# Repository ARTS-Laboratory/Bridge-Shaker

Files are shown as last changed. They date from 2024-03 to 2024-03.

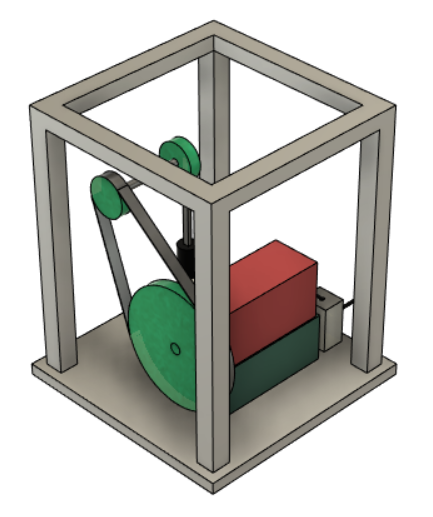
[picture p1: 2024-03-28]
images/design_view2_v2.png

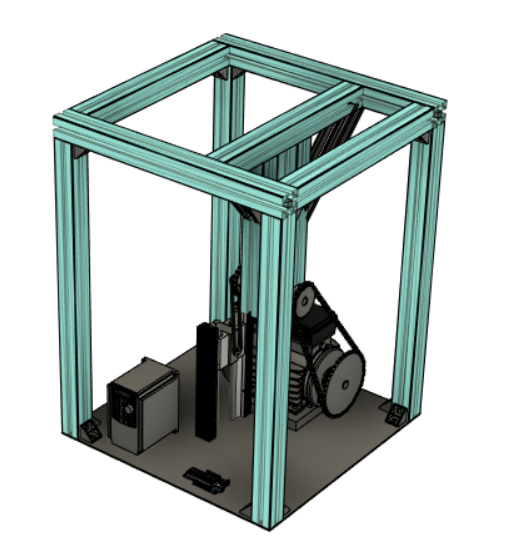
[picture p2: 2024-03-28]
images/assembly_v2.png

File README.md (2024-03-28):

# Bridge-Shaker

A modal shaker for bridges created by the May 2023 Downey1 senior design team.

## CAD files

STEP files of each component of the bridge shaker. Created in Fusion 360 2023, printed with Cura.

## images

Pictures of CAD assembly.

## model

Simulink model of bridge shaker.

## reports

All reports for Senior Design I and II.

## test_data

Data from bridge shaker on 300 main bridge with accelerometers. Tests were performed at 5 Hz, 10 Hz, 11 Hz, 15 Hz, and 20 Hz

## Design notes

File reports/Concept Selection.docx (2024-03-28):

Concept Selection

1. Introduction

The purpose of concept selection is to evaluate each previously generated concept and determine which is the most viable to advance in the design process. The significance of concept selection is that it utilizes empirical measurements to select the best concept for the customer without interference from designer biases. This report presents a matrix-based down-selection of each concept using previously identified selection criteria. First introduced is the concept screening process, which assesses positive or negative concept criteria performance relative to a baseline concept. Once concept screening is completed, this report advances to the concept ranking, which assigns quantitative values to the positive/negative performance of the top concepts from the concept screening. Finally, the chosen concept is presented as the design the team plans to advance to fabrication. All referenced concepts are provided in the appendix and are referenced by their numbers throughout the report.

2. Concept Screening

The concept selection matrix’s main function is to narrow down the options by eliminating concepts that score too low in addressing customer requirements. The selection criteria was based on the customer requirements formulated in the Functional Decomposition and Concept Generation report. Each concept was rated relative to the reference, concept 1, to decide which concepts would be desirable to move forward with. The reference concept was decided unanimously among the group to be the best “middle path” due to its simplistic design and intuitive nature, but other concepts could outperform it due to issues inherent with a spinning weight on a moment arm. In the matrix, a "+” indicates that the given concept would outperform the reference in the customer requirement, while a “-” indicates it would underperform in relation to the reference. A “0” means that it would perform the same as the reference concept. It should be noted that when the table was first created, more selection criteria existed (as shown in the Needs Metrics Matrix in the appendix) but were removed due to similar performance across concepts. This would have given a result of “0” along the entire column, and therefore would not have had any factor in changing the comparative scores. The results of each concept performance are shown in Table 1.

Table 1: Selection Matrix

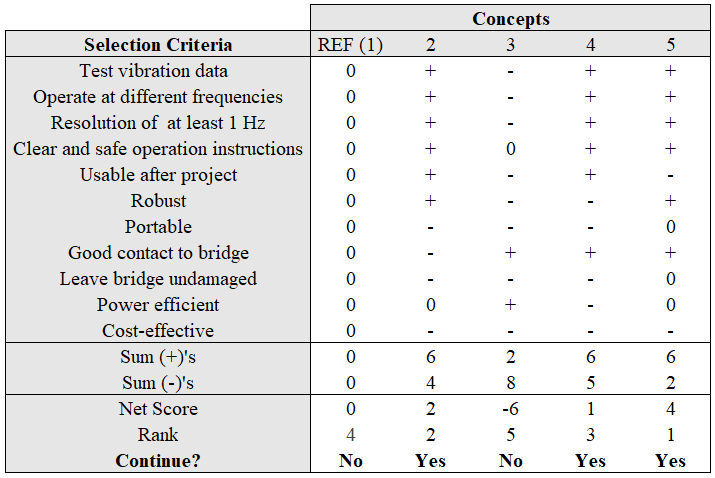
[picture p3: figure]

The final score for each concept was calculated by subtracting the sum of “-”s from the sum of “+”s. The concepts were then ranked based on these scores and the top three scoring concepts moved on to the second round of concept ranking. The ratings were given based on analysis and a vote of each group member comparing each concept with the reference. The top three concepts based on Table 1 are concepts 2, 4, and 5. Concept 2 is the design with solenoids inducing vibration, concept 4 is the hydraulic actuator-based design, and concept 5 is the linearly oscillating weight that is moved up and down with a crank. Concepts 1 and 3 did not have a high enough score to move on to the second round. Concept 1 underperformed in multiple areas, including contact to bridge and operating at different frequencies. Concept 3 underperformed in the categories of clear and safe operation instructions and resolution of at least one Hertz.

3. Concept Ranking

The top three out of five concepts proposed were used to create a concept ranking matrix to condense the list of possible candidates for a final concept. The concept ranking matrix would further derive which design was the best to move forward with. Each concept was given a rating between 1 and 5 based on how well it meets each selection criterion of the project. A rating of 5 indicates a significant improvement from the reference design while a 1 indicates a severe deficit. The importance weight factor was determined by the team in the product specifications report with the Needs Metrics Matrix. The importance weight factors were normalized across the selection criteria (see appendix for normalization formula) and multiplied with the rankings, resulting in a weighted score for each criterion. All the weighted scores for a concept were added together for a total score. The highest total score would be the concept deemed the best to move on with for the project. Table 2 shows the concept ranking matrix and concludes that concept 5, a linear weight with a DC motor, is the best option due to its vast improvement on the reference.

Table 2: Concept ranking with importance weight factors.

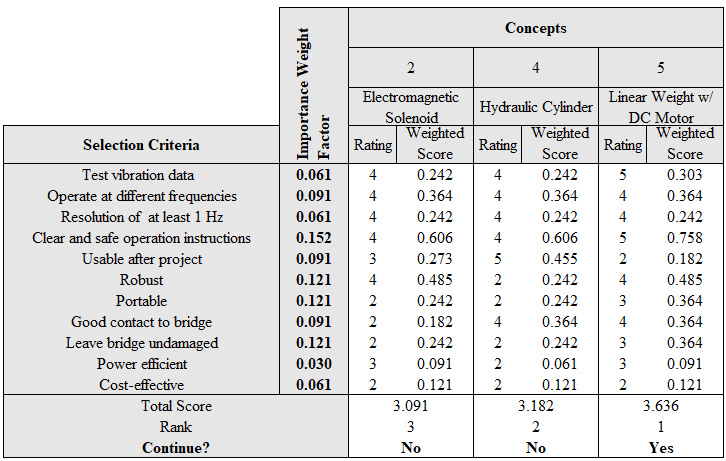
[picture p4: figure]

It was decided that the linear weight with a DC motor would test vibration and be easier and safer to use than the other concepts. The highest importance weight factors corresponded to the clear and safe operation instructions, robust, portable, and leave bridge undamaged selection criteria. Concept 5 ranked higher relative to the other concepts in three out of four of these categories, which explains its higher total score and designation as the best concept.

4. Final Concept

The concept selection tables designated the highest-scoring concept as the best design. Concept 5, the linear weight powered by a DC motor shown in Figure 1, scored highest in both tables because of its ability to test vibration data at a wide range of values, as well as the ability to transfer energy more efficiently to the bridge.

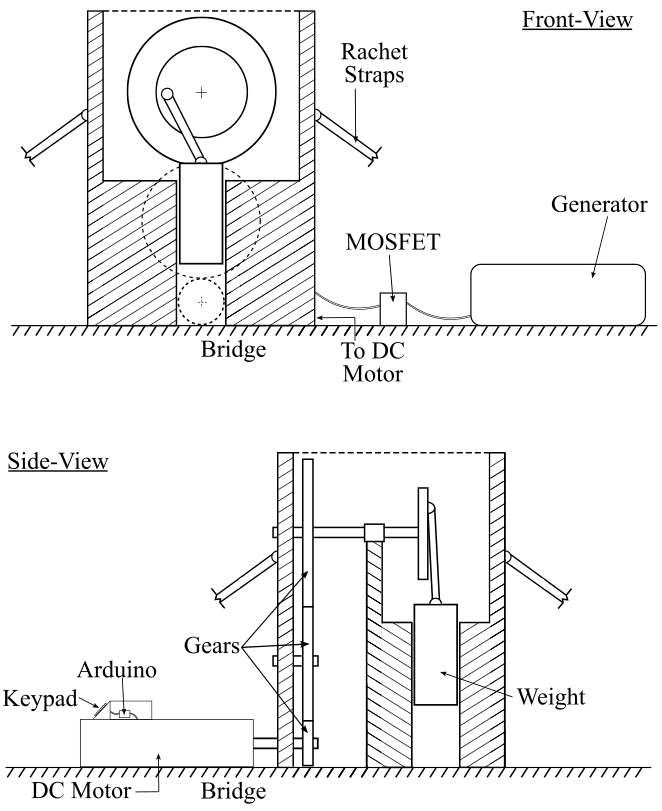
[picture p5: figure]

Figure 1: Excitation via DC Motor and powertrain for linear actuation.

The generator will provide enough power to the system while still maintaining an ease of portability. The MOSFET will control the flow of power from the generator to the DC motor and Arduino. Desired values for frequency and time can be input via the keypad, and the Arduino will control the speed to match the desired frequency. The energy of the DC motor will be translated through the gears and into the weight to create a linear motion, which will transfer downwards via the shaker’s weight into the bridge, inducing vibration. In an interview with stakeholder Joud Satme, he expressed concerns about concept 1’s ability to transfer energy from the shaker into the bridge and how rotational motion would be less efficient because forces were being exerted everywhere around the radius of the weight. Concept 5 can do this more efficiently by using gears to move a weight up and down to localize and create a one-dimensional force. This force would be better suited for testing vibration data because there is minimal wasted energy. This design is more complicated than some of the other concepts, but when evaluating the criteria for a productive shaker, concept 5 prevailed. The power train will add elements of difficulty in the design process, specifically trying to find an efficient gear ratio to excite all frequencies needed while not stalling the motor. To address this challenge, the team will source outside expert advice on gear train design, as well as create prototypes of gear ratios for experimental testing.

5. Appendix

Needs Metrics Matrix

Concept 1

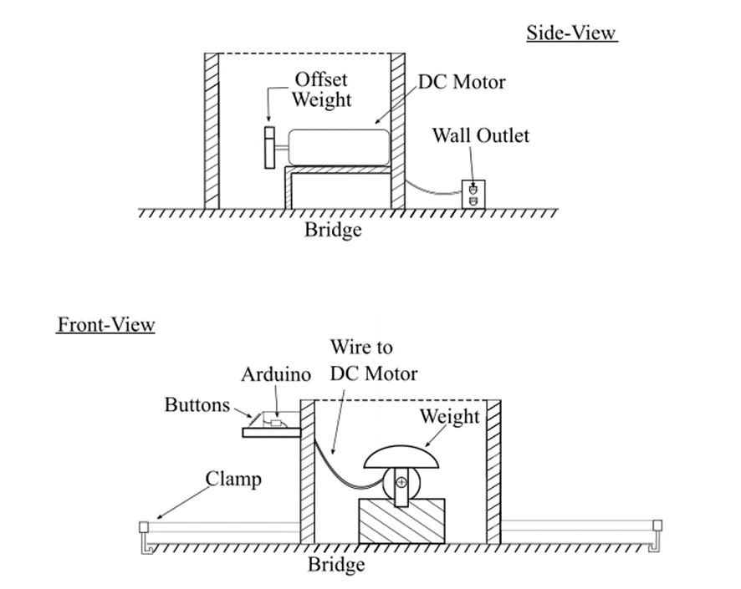
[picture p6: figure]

Concept 2

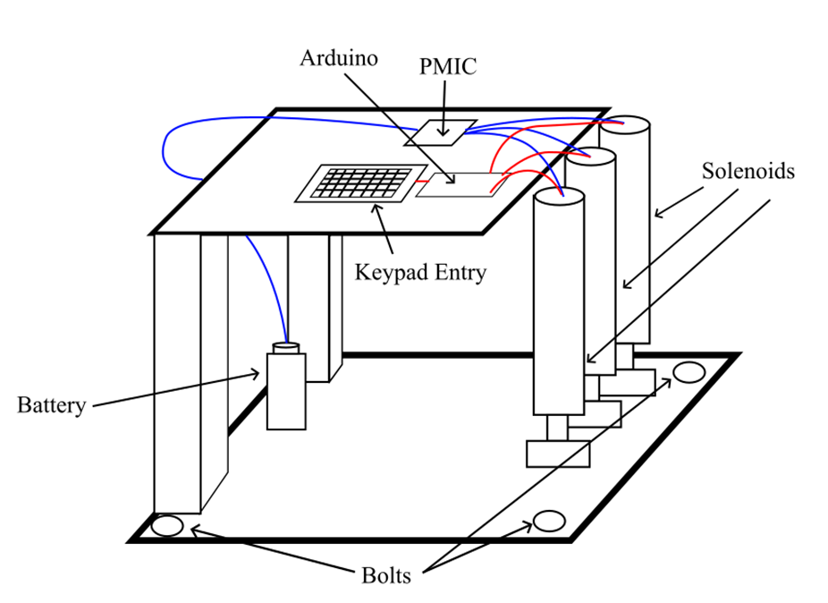
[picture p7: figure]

Concept 3

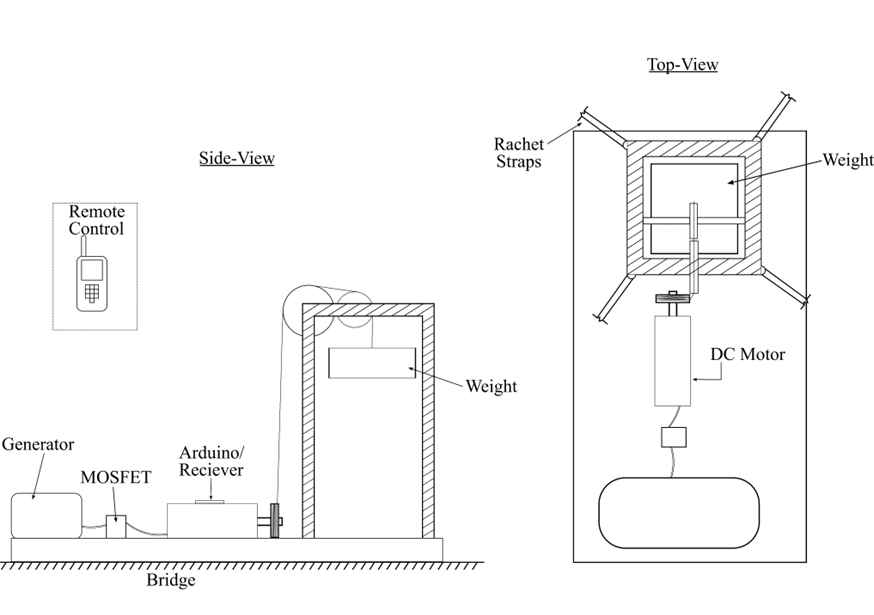
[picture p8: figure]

Concept 4

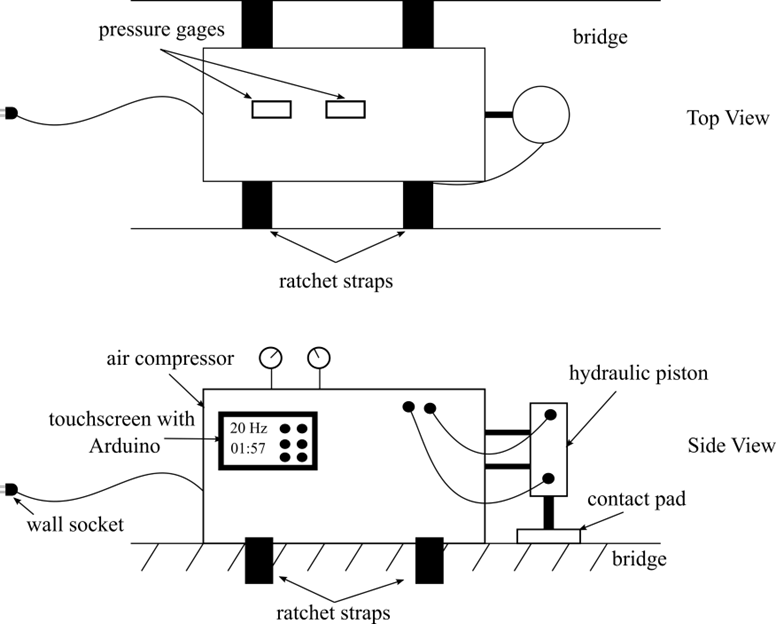
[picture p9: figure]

Concept 5

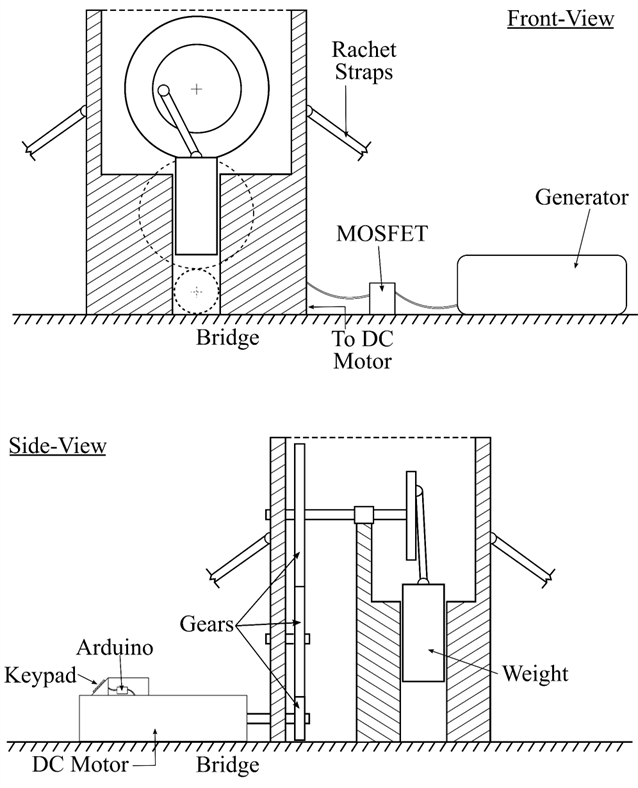
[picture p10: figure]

Normalization Formula

Importance Weight Factor= (Individual product specification weight factor)/(Sum of all product specification weight factors)

Downey1Concept Selection Process and Report11/04/2022

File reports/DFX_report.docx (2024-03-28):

Design Refinement

1. Introduction:

This DFX chapter entails this project’s specific design goals, including the design for manufacturability and assembly, cost, safety, the customer requirements, ease of use, durability/reliability, and serviceability. The design refinements which are being processed entail primarily the assembly and ease of use for the mass shaker. The assembly requires precise, accurate measurements along with the dimensions of the screw fasteners and brackets. Ease of use for the system comes down to programming the VFD and the visual data which will be displayed to the user via tachometer sensors for the shaft holding the weight. Manufacturability is vital because the shaker needs to be assembled and produced within a reasonable amount of time. The cost is also an important part of the design because we cannot go over budget, therefore the group has been using many parts readily available in the ARTS lab. Safety is arguably the most vital requirement, due to not only preventing injury to users of this project in the future, but also avoiding possible liability involved. The reliability/durability and serviceability of the bridge shaker go hand in hand. This project is planned to last without needing servicing for several years (3-5), thus robustness with the sourcing of quality parts is key to this project's success within the ARTS lab. The serviceability for the shaker will be dependent on the methods of securing the parts together, and whether the parts sources will be available in the future.

2. Design for Manufacturability and Assembly

To optimize manufacturability, the team considered material selection and connector design. Off-the-shelf parts were chosen in order to ease sourcing, and parts were chosen considering both cost and replaceability. 8020 40 series extruded aluminum in was chosen due to its ease of assembly. The 8020 series includes support brackets, connectors, beams, and fasteners that are compatible with each other to facilitate the manual assembly process by reducing the number of specialized parts and sourcing as many parts from one company as possible. The main trade off here is that 8020 extruded aluminum is more expensive due to its specialized design, and all connectors will have to be 8020 connectors to pair properly with the beams. The four corner connectors were 3D printed following an 8020 connector CAD model in order to reduce costs and weight; however, the team decided to perform poka yoke on the connectors since they were being printed. Guide channels were added to reduce the stress on the plastic from the screws and make assembly easier by keeping beams in place. In order to ensure the vertical beam is all the way down, the guiderail for the vertical beam was extended so that the two lateral beams would not be placed too far in and obstruct the vertical beam. Figure 1 illustrates the changes made to the brackets. A key tradeoff here is the time required to print the connectors, as well as the reduced strength of PLA versus aluminum.

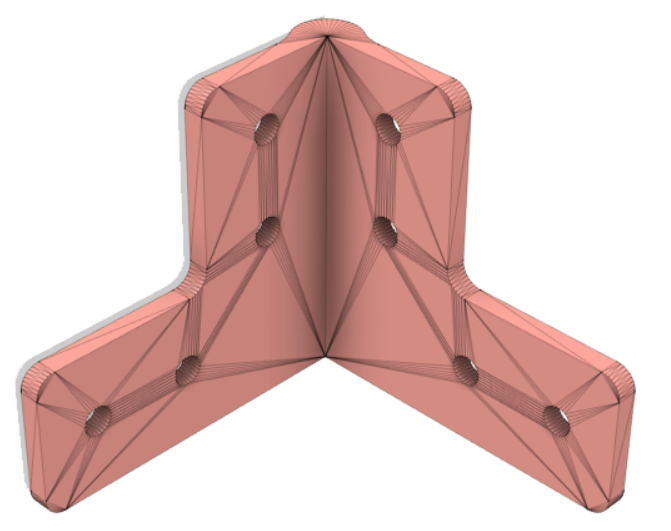
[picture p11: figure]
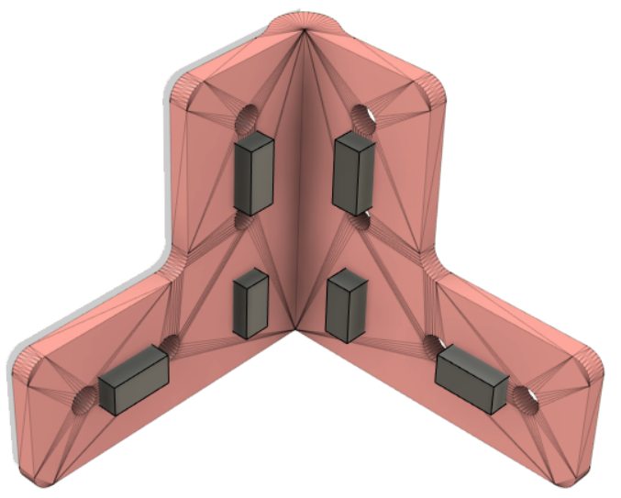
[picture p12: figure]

Figure 1. 3D printed bracket with only spine modification (left) and 3D printed bracked with poka yoke guiderail design.

3. Design for Cost

Cost was a limiting factor for the design team when coming up with ways to produce the shaker for Dr. Austin Downey. Inflationary reasons have made some parts of the build extremely expensive to buy and alternatives had to be sourced out. For example, non-name brand microcontrollers were purchased for the computation of the data and a VFD (Variable Frequency Driver) was sourced from Amazon instead of a big-name product. This saved a few dollars throughout but ultimately ended up reducing the gross amount spent more than expected. Another way the team designed for cost was by trying to use aluminum parts rather than steel parts. The ARTS Lab had an abundance of extruded aluminum for the team to use that reduced the frame production cost to $0. A similar approach was taken to the motor and the brackets. The motor was recycled, with permission, from one of the older projects that are stored in the sub-basement of 300 Main St. This three-phase motor would have been $400-700 (gathered from online stores while sourcing motors) off the shelf, instead the group spent no money on it. Since the brackets for the frame have been designed and 3D printed, the cost for each bracket went from $10-20 apiece, down to virtually $0 thanks to the ARTS Lab’s stockpile of PLA plastic. Lastly, an element of purchasing that saved a fair amount of money was sourcing parts through Grainger and placing a bulk order. Grainger offers free shipping and on larger orders such as the one placed, it saved a favorable amount of money compared to other online parts stores in shipping costs.

4. Design for Safety

Operating a shaker that involves handling a weight through high voltage rotation poses significant safety concerns for any individuals within close proximity during usage. An identified concern is the potential for the vibrational mass shaker to become overly efficient and cause disintegration, thus projecting debris and the weight. To diminish this potential safety hazard, it is crucial to ensure that the shaker is securely mounted onto the bridge, withstanding any forces generated during operation without the risk of tipping over. The design team opted to stabilize the shaker with sandbags to guarantee operational safety. A further concern to consider is the possibility of encountering electrical issues. If the electrical components, namely the motor and VFD, are not correctly wired and grounded, the vibrational mass shaker could pose a potential electrical shock hazard. To preclude these electrical risks, the design team conducted thorough research on wiring diagrams and component datasheets to ensure that all components were appropriately grounded and correctly wired. In order to prevent any of these safety concerns from ever becoming a problem, regular maintenance and inspection of the shaker and its components should be performed to ensure proper operation and determine any potential safety hazards.

5. Design for Customer Requirements

The goal of this project is to design a bridge shaker for Professor Austin Downey and the ARTs lab that will be used to test vibration data by operating at different frequencies. It must be safe to operate and leave the bridge undamaged. The mass shaker will induce vibrations via an oscillating weight which will transfer that energy to the bridge. The Needs Metrics Matrix, shown in Figure 2, has remained stagnant throughout the design and assembly process, with the most important engineering characteristics still being adaptability, usability by others, and product details. The contact area and weight of the shaker have been refined to have more emphasis on total product weight at the expense of the contact area, which will still be sufficient to transmit the force as the product will still be fully on the bridge, with the force increasing at the frame components in the base due to less material that would dissipate it.

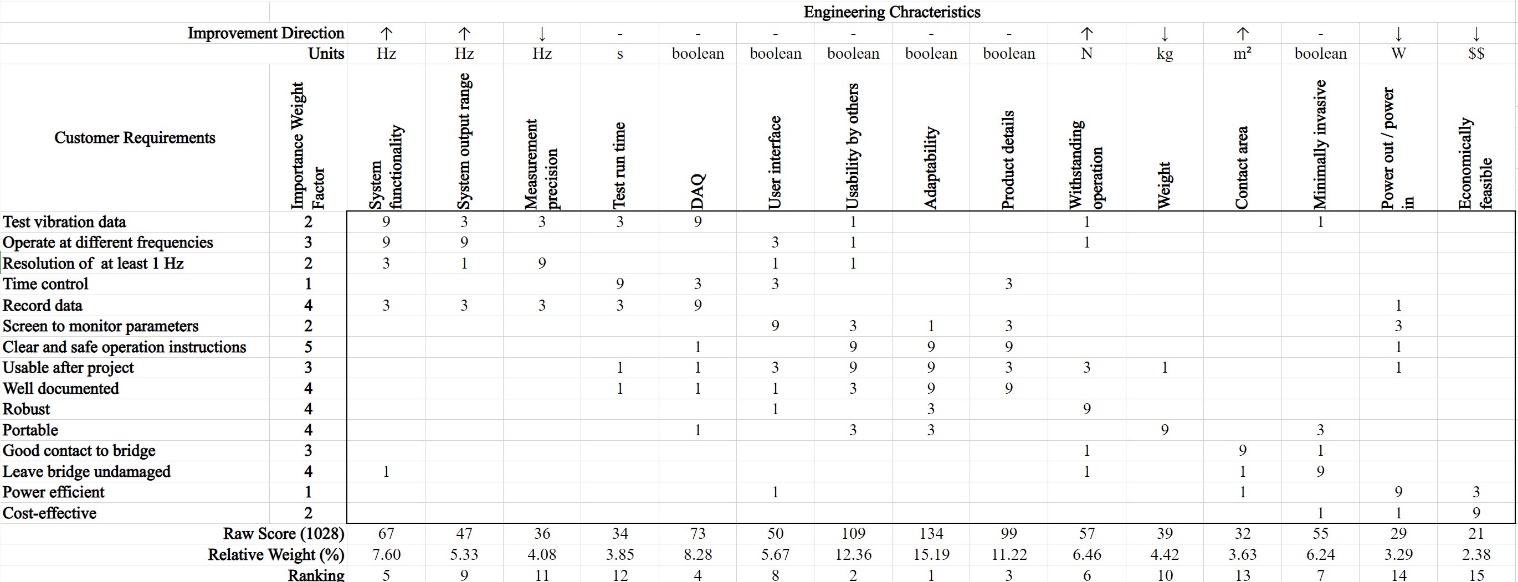
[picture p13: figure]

Figure 2. Needs Metrics Matrix shows the top engineering characteristics of importance along with customer needs.

5a. Design for Ease of Use

Ease of use was chosen because the Usability by Others EC was rated number 2 in the Needs Metrics Matrix. To enhance user experience, an external Arduino is added to clearly show the frequency and duration of the test. The VFD reads all user input to control the motor speed, but the data it shows is for the motor rather than for the weight. The external Arduino uses sensors to obtain and show the desired parameters for ease of use. The main tradeoff of having the Arduino is power consumption, as it requires extra power just for itself. Additionally, the shaker is entirely open-source with an extensive GitHub to promote user understanding and adaptability. The tradeoff of having the project open-source is that it would be less profitable in a market as competitors could recreate the design, but that is not a concern for the sponsor.

5b. Design for Durability/Reliability

To ensure the durability and reliability of the vibrational mass shaker, the design team prioritized the selection of high-quality materials and components. The frame of the shaker, constructed from high-strength 8020 series extruded aluminum, was chosen to withstand the significant forces exerted during operation and provide resistance to corrosion and wear. The metallic components, including gears, links, and weight, were similarly selected for their durability and longevity, with either steel or aluminum materials used. The 3-phase AC motor chosen for the shaker was a high-quality component that is expected to function optimally for the entire operational lifespan of the shaker. Coupled with a reliable and functional VFD, these components provide a robust and dependable vibrational mass shaker, which is engineered for long-term use.

5c. Design for Serviceability

The shaker will be a relatively violent machine that will attempt to vibrate itself into pieces. For this reason, the team attempted to minimize the parts used and design a shaker that was robust enough to remain strong even under the immense stress of the vibrations. With this comes the fear of part degradation or even failure. The team has sourced commercial products for the gears, shafts, frame, linkages, bearings, etc. this way anyone using the shaker after it has been commissioned can easily source a part to repair the shaker. Additionally, everything purchased, changed, or installed will be documented in a repository on GitHub that will allow for a new user to understand the device and be able to make simple repairs with ease. The only foreseeable serviceability concerns are with the motor and the VFD. These two items cannot be worked on explicitly like the other parts of the shaker. The VFD will have to be sourced out and purchased again if it were to break. The motor was recycled from an old project so it is likely that another motor would need to be sourced if the current one breaks.

6. Conclusions [and/or] Recommendations

Major refinements to this project mainly occurred in the layout and method of connecting parts to the frame, as well as refining the design of the brackets to increase robustness. Only minor changes were made to the sourcing of parts for the drive train, mainly the shaft and the sleeve which will be secured to the frame. The dimensions for the sprockets have remained constant, as well as the method of meshing them together via chains. The chain method will allow for flexibility of motor/sprocket replacement, especially if the dimensions of the motor or sprocket change. Further inspection of product safety may deem that the addition of surrounding walls for the shaker may be necessary in case of an unexpected failure in one of the moving parts. Tradeoffs have occurred primarily in the mass shaker’s base. While it needs sufficient contact to the bridge with a solid frame to place the components, too much weight on the bottom will ultimately affect the ergonomics of the product. An entirely metal base would also increase the price of the project, while providing no benefits to the wasted space. The method of stabilizing the shaker has also been changed from ratchet straps to sandbags on protruding extruded aluminum connected to the frame. This will give the shaker more vertical stability than the original horizontal, which is completely logical considering the acting force is strictly vertical. This method will also ensure the rachet straps wouldn’t end up pulling the shaker apart by slowly warping the frame, and users cannot accidentally over tighten them and break the shaker.

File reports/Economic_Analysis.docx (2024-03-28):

Economic Analysis

1. Introduction

Evaluating the economic gain or loss of a certain product is a vital aspect of engineering analysis. Ensuring that the product will have a net positive gain and not be a ‘money pit’ is done by evaluating the current assembly costs and operating costs coupled with the yearly expected expenses tied to maintenance and operation. The shaker being for Dr. Austin Downey and company has no industry value as this is a ‘one-of-a-kind' product that is designed specifically for the students who are testing the structural integrity of bridges and walking paths. The monetary value for this product can be estimated through the possibility of grants being offered to the students for research in this field. Given this fact, the break-even analysis, variable cost of labor, “year zero” cost, and the cost reduction analysis will be estimated using reasonable values. This analysis will also cover the expenses incurred and compare them to the expected future value of the parts most often replaced.

2. Costs, Savings, and Revenues

The bridge shaker being designed by Downey1 is intended to be an academic tool rather than a commercial product; however, the value of this shaker lies in the grant money that stands to be awarded by using the shaker for long-term vibration testing on large structures, something the ARTS Lab does not currently have equipment for. The costs are primarily from materials, as the labor required to build the shaker can be delegated to lab researchers. The cost for a single prototype is broken into fixed (materials, manufacturing/assembly) and variable costs below, and are modeled assuming the product would be commercially sold. This means that technician labor is estimated rather than researcher labor, and all parts are sourced from professional suppliers. Table 1 shows the fixed costs for a single bridge shaker based on the current prototype.

Table 1. Fixed costs per unit of current prototype.

Materials
Description | Cost (USD) | Quantity | Source
3 Phase AC Motor | 705.18 | 1 | Grainger
Industrial Chain | 29.55 | 1 | Grainger
Shaft pinion, 4" | 40.00 | 2 | Grainger
Motor gear, 8” | 64.58 | 1 | Grainger
Keyed Shaft: 1 in Dia, Aluminum | 52.63 | 1 | Grainger
Aluminum 80/20 40 series, 1 ft | 15.44 | 18 | Grainger
Elegoo Uno R3 | 17.99 | 1 | Bill of materials
LCD | 5.99 | 1 | Bill of materials
3pin IR Infrared Module | 1.89 | 2 | Bill of materials
OSH Park custom PCB for sensor input to Arduino UNO (shield form factor) | 23.55 | 1 | Bill of materials
Shaft bearings | 26.79 | 2 | Bill of materials
Extension cord | 25.98 | 1 | Bill of materials
Weight, aluminum 4 kg | 9.89 | 1 | Grainger
80/20 40 series fasteners | 1.54 | 100 | McMaster Carr
VFD, 230 Volts, 1 to 3 Phase | 118.84 | 1 | Bill of materials
PLA 3-way bracket | 2.52 | 6 | Cura 3D printer slicing estimate (101 g PLA per unit)
PLA triangle bracket | 1.42 | 20 | Cura 3D printer slicing estimate (57g PLA per unit)
Total: | 1666.98

Manufacture/Assembly
Description | Cost | Quantity | Source
Machining labor (2D cutting) | 20.00 | 2 hours | Wade 2022
Assembly labor | 18.81 | 5 hours | Indeed 2023
Total: | 134.05
Total fixed cost: | 1801.03

The total fixed cost per one bridge shaker is $1,801.03. It is important to note that for the shaker built by Downey1, many parts were able to be sourced for free, including the AC motor and Arduino. In the case of commercial production, this is a reasonable fixed cost considering the size and scale compared to other modal shakers. Table 2 displays the variable costs per year of the shaker.

Table 2. Variable costs per unit per year of current prototype.

Description | Cost | Quantity | Source
Maintenance | 18.81 | 20 hours | Indeed 2023
Operational electricity | 14.54/hr | 0.15 hours per test, assume 50 tests | Dominion Energy 2021 (0.021086 per kWh, at 690W)
Total variable cost: | 485.25

The total variable cost per year is approximated at $485.25. This estimate assumes 50 ten-minute tests per year and 20 hours of maintenance over the year by the same technicians responsible for the assembly of the shaker in the fixed costs. The predicted lifespan of the bridge shaker is 3 years, assuming proper pre-test maintenance (tightening fasteners, lubrication). Table 3 shows the up-front cost of the shaker.

Table 3. Up front (“Year Zero”) costs.

Description | Cost | Quantity
Research and development | 50.00/hr | 90 hours
Creality 3D printer | 236.00 | 1
Total Year Zero cost: | 4736.00

The up-front project costs total to $4,736.00 and are primarily the cost of design consulting with the team. The cost of the printer is included as an equipment cost, but the cost of the machine that manages 2D cutting of the aluminum is not included because the task is outsourced to machinists.

Table 4. Reduced cost of the materials for a version of the shaker.

Reduced Cost Version of Materials
Description | Cost (USD) | Quantity | Source
3 Phase AC Motor | 705.18 | 1 | Grainger (Dayton)
Industrial Chain | 15.32 | 1 | McMaster Carr
Shaft pinion, 4" | 40.00 | 2 | Grainger
Motor gear, 8” | 64.58 | 1 | Grainger
Keyed Shaft: 1 in Dia, Aluminum | 45.15 | 1 | McMaster Carr
Aluminum 80/20 40 series, 1 ft | 15.44 | 18 | Grainger
Elegoo Uno R3 | 8.96 | 1 | eBay
LCD | 5.99 | 1 | Bill of materials
3pin IR Infrared Module | 1.89 | 2 | Bill of materials
OSH Park custom PCB for sensor input to Arduino UNO (shield form factor) | 23.55 | 1 | Bill of materials
Shaft bearings | 26.79 | 2 | Bill of materials
Extension cord | 25.98 | 1 | Bill of materials
Weight, aluminum 4 kg | 9.62 | 1 | McMaster Carr
80/20 40 series fasteners | 1.54 | 100 | McMaster Carr
VFD, 230 Volts, 1 to 3 Phase | 118.84 | 1 | Bill of materials
PLA 3-way bracket | 2.52 | 6 | Cura 3D printer slicing estimate (101 g PLA per unit)
PLA triangle bracket | 1.42 | 20 | Cura 3D printer slicing estimate (57g PLA per unit)
Total: | 1635.97

Table 4 includes material cost reductions in terms of money on parts. It is important to note that the reduction is not substantial as the team was trying to optimize costs for the current prototype already. However, there were some significant optimizations when sourcing some materials, such as the keyed shaft, from McMaster Carr rather than Grainger. There are cheaper options for building a frame such as welding materials together, but the team found that unnecessary as the shaker would need to have the option to be taken apart. As sourcing cheaper materials will not change the cost of labor for assembly, the cost of assembly will stay the same at $134.05. This would bring the reduced total fixed cost to $1770.02, having around a 2% reduction in cost. An option for increasing longevity and reducing the need for maintenance would be to source aluminum brackets to replace the PLA. This would increase the cost of the triangle brackets from $1.42/bracket to $21.99/bracket and the 3-way bracket from $2.52/bracket to $10.99/bracket when sourcing from Amazon.

3. Analysis

Break-Even Analysis:

The bridge shaker is planned to be a viable tool in engineering work for 10 years. This period was chosen because at that point the research performed with the shaker will most likely be completed and the project will have turned a project in the break-even analysis, which was performed to determine when the revenue would surpass the cost along with initial startup. The following values were considered in Table 5.

Table 5. Break even analysis conditions.

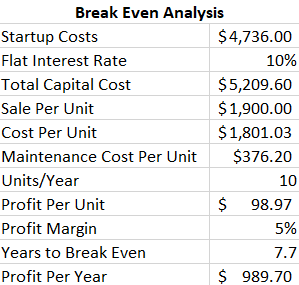
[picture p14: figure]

These values are assuming the shaker is relatively low demand, only producing 10 a year and requiring yearly maintenance for upkeep. The shaker’s price is set at $1,900, which makes about a 5% profit per sale. With these variables, Figure 1 shown below shows the method by which the break-even point was determined.

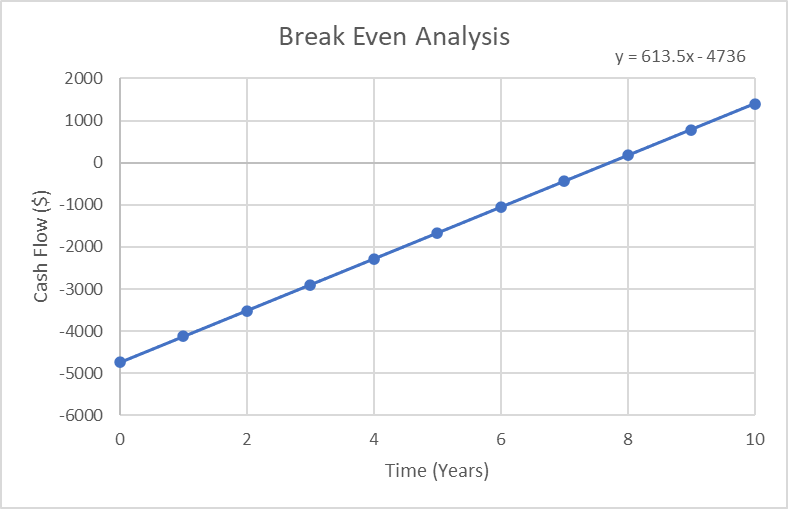
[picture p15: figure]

Figure 1. Break-Even Analysis

As shown above in Figure 1, the equation of the trendline can be used to estimate the year this project breaks even at 7.7 years. This is unfavorable as the use for this project is for short term research applications. The cash flow diagram of this project is shown below in Figure 2, with the initial cost of startup at year 0, and every year, having costs to produce 10 shakers a year. The profits each year come from the sales of 10 shakers each year.

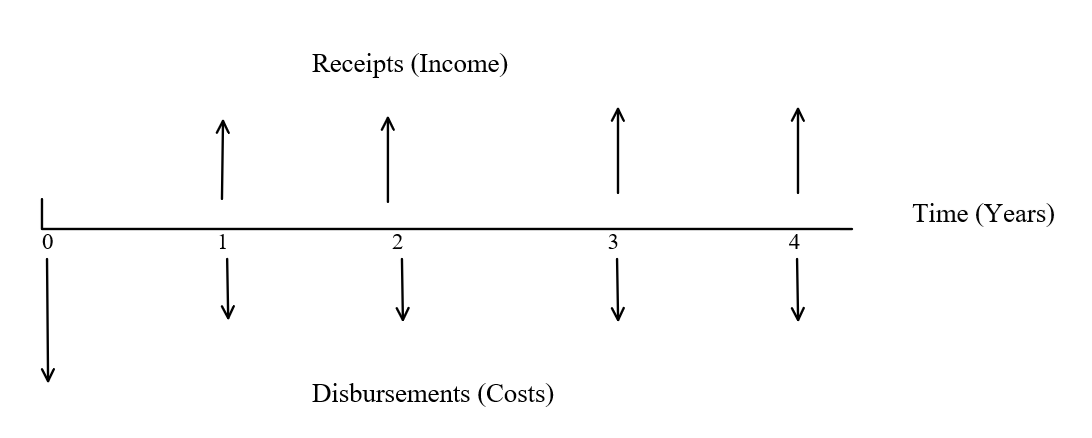
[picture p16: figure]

Figure 2. Cash flow diagram

Net Present Value:

The Net Present Value represents the difference between the present value of cash inflows and outflows over a specified period. It is used to analyze the profitability of the project over its life cycle/useful lifetime [4]. The equation used to determine the present value for each year is shown below as Equation 1.

NPV= ∑_(t=1)^T (C_t)/((1+r)^t)-C_o Eq.1

In this equation, NPV is the net present value, t is the period, starting at 0 and stretching over its life cycle until year 10, C_t is the net cash inflow of the period, r is the discount rate, and C_o is total initial investment cost. In order to find the discount rate, the NPV equation must be set to 0, and the other values are known besides r as shown below in Table 6.

Table 6. Values for the NPV Equation

Variable | Value
t | 10
C_t | 98.97 × 10
C_o | 4,736
NPV | 0

With these variables all know and r unknown, the discount rate can be calculated to be 14.5%. Finally, the NPV can be calculated as shown in Table 7 below.

Table 7. NPV Calculation

Net Present Value
| Project Time (Years) | 10
| Discount Rate | 14.5%
Year | Present Value
0 | -$4,736.00
1 | $5,600.37
2 | $5,490.91
3 | $5,395.31
4 | $5,311.81
5 | $5,238.89
6 | $5,294.66
7 | $5,119.59
8 | $5,071.01
9 | $5,028.59
10 | $4,991.53
Total Net Present Worth | $47,806.67

As shown above, the net present worth of the project can be estimated to be $47,806.67. This is a favorable outcome and could hold opportunity to be profitable. However, this project is not meant for something to be in mass production. While the sourcing of the parts was relatively easy, the fact of the matter is there is no way of knowing the demand for the product, which has means only to serve the ARTS lab in conducting experiments dealing with constant impulse-induced vibrations. While there could be universities that would like to fund this and may want to purchase a shaker for these reasons, there is no guarantee that the market would be there. Additionally, the shaker is designed to last for at least 10 years with relatively minimal maintenance besides replacements for parts which are under the greatest stress. Therefore, it is advised to keep this as a small scope project for the purposes of the University and research grants that come in for which this shaker can be used to aid in its development.

4. Conclusions/Recommendations

In conclusion, the bridge shaker is expected to be useful for three years until research is completed. A break-even analysis was conducted to determine when revenue would exceed costs by assuming low demand, a production rate of 10 units per year, and yearly maintenance. The shaker is priced at $1900, resulting in a 5% profit per sale. The break-even point is estimated to be 7.7 years based on the trendline equation.

List of References

1. Wade, A. O. (2022, September 20). How much does CNC cost per hour? www.remodelormove.com. https://www.remodelormove.com/how-much-does-cnc-cost-per-hour/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
2. ‌Indeed. (2023, March 15). Assembly technician salary in United States [Review of Assembly technician salary in United States]. Indeed. https://www.indeed.com/career/assembly-technician/salaries
3. ‌Dominion Energy. (2021, December 9). Schedule 1-Basic Residential Rate [Review of Schedule 1-Basic Residential Rate]. Dominion Energy. https://www.dominionenergy.com/-/media/pdfs/virginia/residential-rates/schedule-1.pdf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
4. Fernando, J. (2022, November 16). Net present value (NPV): What it means and steps to calculate it. Investopedia. Retrieved March 20, 2023, from https://www.investopedia.com/terms/n/npv.asp

Downey1Economic Analysis Report03/20/2023

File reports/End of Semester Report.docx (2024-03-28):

End of Semester Status Report

Statement of last Month’s Goals:

- Present a summary of product needs, specifications, and functions to sponsor, as well as five proposed and one final project design in the Conceptual Design Review
- Generate a product architecture report detailing modularity in the design, interactions of different functional clusters, and presenting visuals of the product layout and a CAD model of the chosen design
- Present a refined design to the sponsor in the Preliminary Design Review
- Determine desired motor to drive the weight
- Create a project budget and source parts
- Determine a project timeline for next semester

Progress:

Most of the tasks were completed. We are still in the process of determining the desired motor to put into the shaker. This task may take some time at the beginning of the next semester while we are in the process of prototyping. The strategy for resolution of this problem is to run motors through Simulink simulations and find the perfect motor to run a bridge shaker of our shaker’s size and weight.

Challenges:

Some challenges posed for the linear weight design will be the sleeve that will house it and the method of lubrication for the moving parts to keep them undamaged. We have looked at guide rails to possible use in conjunction with the sleeve to minimize wear. The other challenge is with regards to choosing the right motor, as of right now we have the general specifications for the motor narrowed down but are still looking for one that can be bought at a price range acceptable to Professor Downey. The final challenge is creating a suitable frame for the shaker, we are looking at mostly using aluminum, which will be welded to ensure parts will not shake loose.

Goals:

The TBD’s to be resolved are the motor which will be used, the method of housing and friction reduction for the weight, and the bearings which will be used for the shaft. The motor will be purchased with the aid of Professor Downey and the specifications for it which the Simulink model was used for. The friction reduction and weight housing methods will also be discussed with Professor Downey, but a guide rail system looks viable. The bearings for the shaft are less important at this point but will also be narrowed down when we are closer to construction. We will also be testing the accelerometers on the bridge before we use them on the bridge in conjunction with the shaker.

Purchasing:

Due to the TBDs, the motor is not ready to be purchased until accelerometer testing is performed and the required rpm of the motor is determined. The attached budget has an estimated price of 400 USD for the motor based on past research as it is still TBD. Some items are ready to be purchased, including all the electronics, sensors, and housing material. These purchases will be handled by the team through the responsible students in Dr. Downey’s lab.

Final Concept:

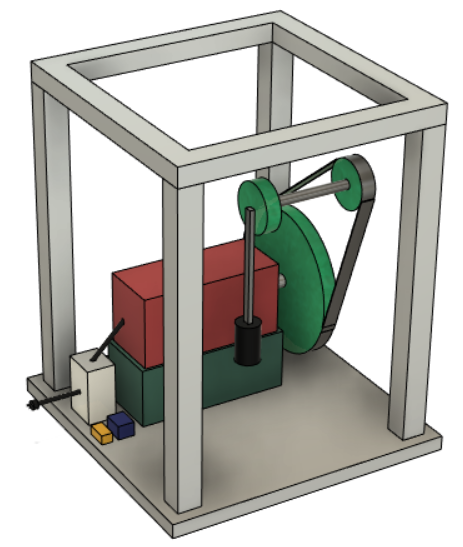
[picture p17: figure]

Figure 1. Side views of final concept.

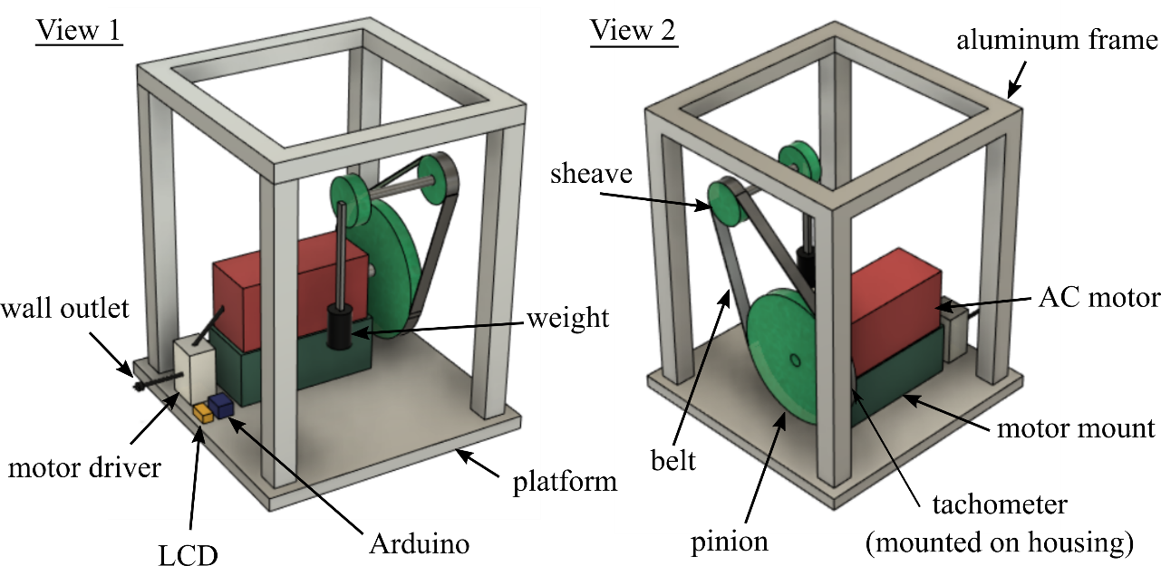
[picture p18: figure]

Figure 2. Labeled views of the selected concept

Proposed Bill of Materials

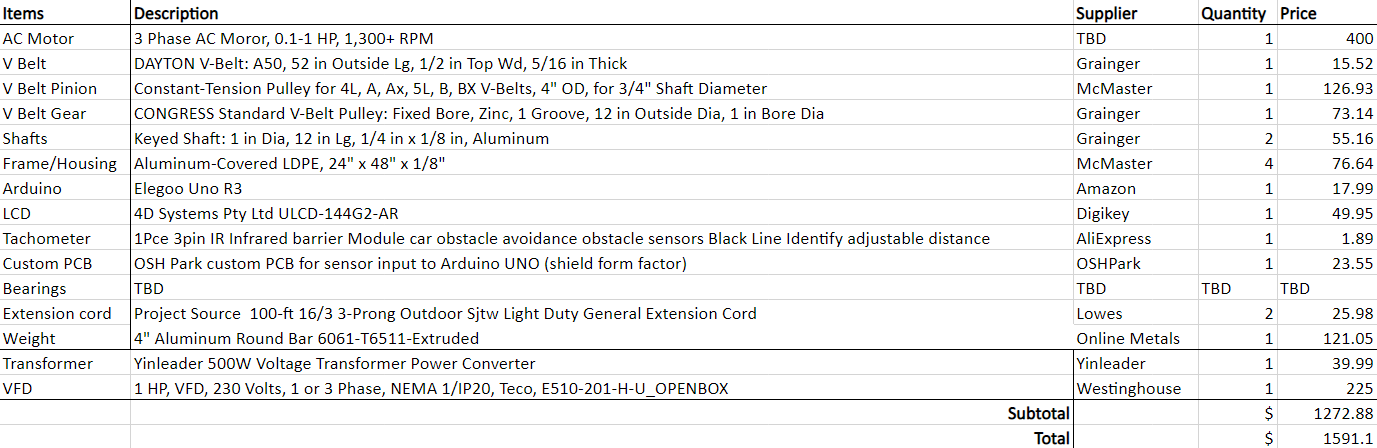
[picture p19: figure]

Project Scope and Budget Agreement

1. Scope of the project defined:

The student design team will construct a prototype of a bridge shaker that tests vibration data, operates at different frequencies, is safe to operate, and leaves the bridge undamaged. The prototype will feature a shaking weight that will transfer energy to the bridge with user control of a motor driver and feedback supplied by in-house sensors.

2. Deliverables:

a. The prototype will be turned over to the sponsor by April 25, 2023

b. The associated GitHub will be fully documented and publicized by April 25, 2023 containing: STL files, Arduino code, operation instructions, build designs/instructions, models, bill of materials

3. Agreed project budget amount

The bill of materials determined by the design team must not exceed $1591.10. This is the total calculated project cost with a 25% increase for contingencies and shipping. Once agreed upon, budget changes must be taken to Dr. Downey directly and approved by Dr. Downey before implementation.

4. Statement of who is responsible for purchasing/acquisition

Purchasing will be a joint effort between the project sponsor, Dr. Downey, and the design team. All components will be brought to Dr. Downey’s attention before purchasing. The design team oversees sourcing parts and components that suit the needs of the project sponsor and will find the most reasonable items for purchase.

5. Statement of who is responsible for machining/fabrication/assembly

The design team oversees machining and fabrication whether it be in-house or sourcing a machinist to complete the work. All other assembly will be completed by the design team at or before the specified deadlines. If there is an issue with any of the above, the design team will notify Dr. Downey and arrangements will be made to solve the issue in a timely manner.

Due to the rigid and short timeline associated with this project, there will be no substantial changes to the scope of the concept or deliverables once both parties (project sponsor and student design team) agree on the above items.

Sponsor Signature: ______________________________________ Date: ____________

Team Member 1: _______________________________________ Date: ____________

Team Member 2: _______________________________________ Date: ____________

Team Member 3: _______________________________________ Date: ____________

Team Member 4: _______________________________________ Date: ____________

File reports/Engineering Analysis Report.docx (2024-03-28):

Engineering Analysis

1. Introduction:

This report contains details of engineering analyses performed to determine theoretical limitations of the bridge shaker at areas of concern. The team brainstormed ways that the bridge shaker could either underperform or fail to identify these areas of concern. Emphasis was placed on failure modes on the consumer end, rather than failure modes during manufacturing. The main concerns are as follow:

A. The product could disassemble itself at the connection joints under the strain of vibratory loads, with either loosening the connection bolts or completely breaking the bracket.
B. Friction in the shafts could lead to underperforming.
C. Friction on the guiderails could lead to underperforming.
D. The guiderail system might not be strong enough to withstand the forces of the weight at max speed, causing it to break and could cause catastrophic damage to the structure. Material selection is important.
E. The VFD could underperform and output less voltage than is needed for the motor.
F. A fuse might trip and cut power to the system.
G. The motor could overheat.
H. The motor might not produce enough speed to provide adequate force to the bridge.

Once the main concerns were identified, an FMEA was used to determine how deeply each failure mode needed to be addressed. FMEA was chosen due to the complexity and diversity of subsystems, as well as its emphasis on safety issues. The results of the FMEA are shown in the table below, Table 1.

Table 1: Failure Modes and Effects Analysis

Failure Mode | Severity | Occurrence | Detection | RPN
A | 10 | 8 | 2 | 160
B | 4 | 6 | 3 | 72
C | 4 | 6 | 3 | 72
D | 10 | 7 | 1 | 70
E | 7 | 4 | 1 | 28
F | 6 | 2 | 3 | 36
G | 7 | 9 | 3 | 189
H | 7 | 7 | 2 | 98

The FMEA shows that the greatest concerns are that the product could disassemble itself at the connection joints under the strain of vibratory loads, with either loosening the connection bolts or completely breaking the bracket; the motor could overheat; and the motor might not produce enough speed to provide adequate force to the bridge. The corrective actions for each of these designs will be determined by conducting engineering simulations. For failure mode A (referred to as failure mode #1), a stress analysis is of the 3D printed joints is run to determine deflection caused by the force of vibration. For failure mode H (referred to as failure mode #2), a Simulink model of the motor drive train subsystem is created to test output force, speed, and effect of gear ratio. For failure mode G (referred to as failure mode #3), thermal ports are added to the existing Simulink model to test motor temperature.

2. Analyses performed

Failure mode #1: 3D printed joint failure.

The first analysis performed was the simulated stress on the bracketing assemblies in Fusion 360. This analysis was needed to ensure the 3D printed brackets could withstand the stress of operation, specifically the shear and bending stress. 3D printed brackets were requested by Dr. Austin Downey because they are cheaper than ordering the alternative metal brackets, and he feels that they should be strong enough to hold the frame together. With this information, the team tested the brackets in simulation. The test was done using a few equations from the textbook Machine Elements in Mechanical Design (not all equations used in the simulation will be listed as the team has no way to find every equation used, the general equations for this type of engineering problem are assumed).

σ=F/A (Eq. 1)

σ=(M∙I)/c (Eq. 2)

ε=σ/E (Eq. 3)

∆L=ε∙L_0 (Eq. 4)

Table 2: Definition of variables for failure mode 1

Variable symbol | Variable name/description | Variable units
σ | Stress | MPa
ε | Strain | N/A
E | Young’s Modulus | GPa
∆ L | Change in length | m
L_0 | Initial length | m
F | Applied force | Pa
A | Area | m^2
M | Bending moment | N∙m
I | Moment of inertia | ￼
c | Distance from neutral axis | m

Knowing these equations and an initial set of parameters based on the orientation of the bracket within the total assembly, the team can constrain and place forces accurately within the simulation. The locked constraints belong to the tops and bottoms of the screw holes in the bracket. The force is comprised of two components: the axial force from the side-to-side movement of the frame and a bending force created by the shaft and weight being supported from the top. Since the software does a comprehensive analysis of the piece and evaluates every section of the bracket, the team cannot give every input condition. The team can supply the image of the constraints placed on the bracket and the forces and their numerical values that were used in the simulation.

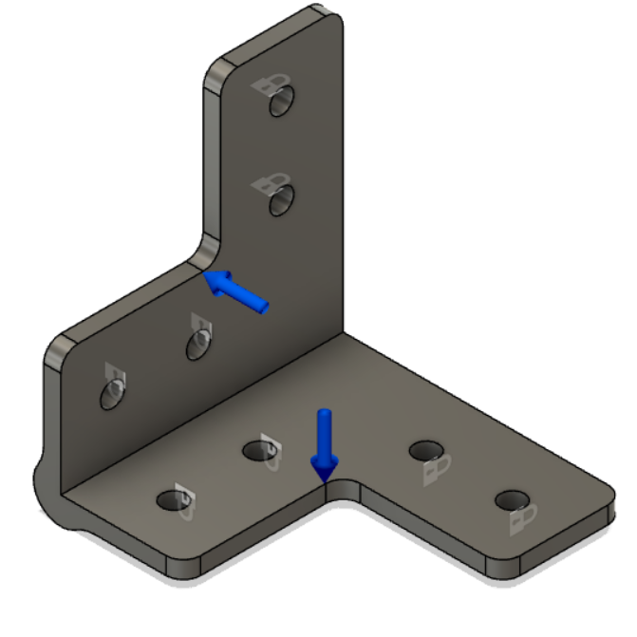
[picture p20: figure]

Figure 1: Constraints and loads on 3D printed bracket.

Each blue arrow in Figure 1 is representative of a force applied to the entirety of the inside faces of the bracket. This is to simulate the force applied from the vibrations induced by the motor. The force value is 3000 N, which is estimated from a Simulink model as a good testing range. The working force is expected to be around 500 N with the maximum output in a worst-case scenario at 6000 N. The team has chosen to throttle back the motor and keep it within a safe operating range. This will provide an accurate estimation to the displacement of the material and the stresses it will undergo. Lastly, the safety factor of the brackets will be simulated. Since the brackets are the main failure points identified by the team, they need to be engineered to not only minimally support the forces of the device, but also be able to withstand greater forces than expected. A high safety factor estimation will confirm or deny this hypothesis.

Failure Mode #2: Output Force

The next failure mode will be simulated via Simulink in MATLAB, which models the resulting output force the weight could supply to the system given the motor specifications and gear ratios. The motor specifications are found on the manufacturer’s site [1]. There are several assumptions and unknowns that must be estimated for the model. For instance, exact inertias of the gears, shaft, etc. are assumed to be negligible due to the nature of the model, with the only source of inertia assumed to be from the slider-crank mechanism. The model also assumes an ideal voltage source, and negligible friction effects on all moving parts. For other model inputs in the system, the slider stiffness and damping are also assumed to be negligible. The inertia of the slider-crank can be estimated in the absence of angular acceleration at the instant of maximum torque. The system will be observed as seen in Figure 2.

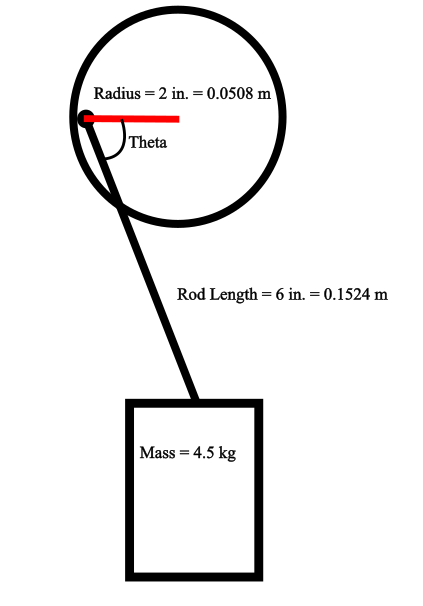
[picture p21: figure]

Figure 2: Free Body Diagram of weight effecting inertia on the system.

Under negligible angular acceleration, the general equations to solve for the inertia of the crank system, neglecting the disk’s mass are shown below [2].

τ=I⋅α; α=1 (Eq. 5)

τ=r×F (Eq. 6)

F=m⋅a (Eq. 7)

cos(θ)=(adjacent side)/(hypotenuse) (Eq. 8)

Table 3: Definition of Variables for Inertia Equations

Variable symbol | Variable name/description | Variable units
τ | Torque | N⋅m
I | Inertia | kg⋅m^2
α | Angular Acceleration | 1 (rad)/(sec^2)
r | Disk Radius | m
m | Mass | kg
F | Force | N
a | Acceleration due to gravity | 9.81 m/(sec^2)
θ | Angle in Figure 2 | deg

Through this calculation, a rough estimate for the crank inertia, calculated to be 2.11 kg⋅m^2 , can be plugged into the Simulink model. The simulation is based on fundamental equations for gear and motor systems, shown below [3].

(ω_1)/(ω_2)=(n_1)/(n_2)=(d_2)/(d_1)=(T_2)/(T_1)=(τ_2)/(τ_1) (Eq. 9)

a_t =α⋅r (Eq. 10)

Table 4: Definition of Variables for Simulink Model Equations

Variable symbol | Variable name/description | Variable units
ω | Angular velocity | (rad)/(sec)
n | Gear speed | RPM
d | Gear diameter | m
T | Number of gear teeth | -
τ | Torque | N⋅m
a_t | Tangential acceleration | m/(sec^2)
α | Angular acceleration | (rad)/(sec^2)
r | Radius of disk | m

These equations govern the calculation of output force on the system, the diagram for the Simulink model can be seen in Figure 3.

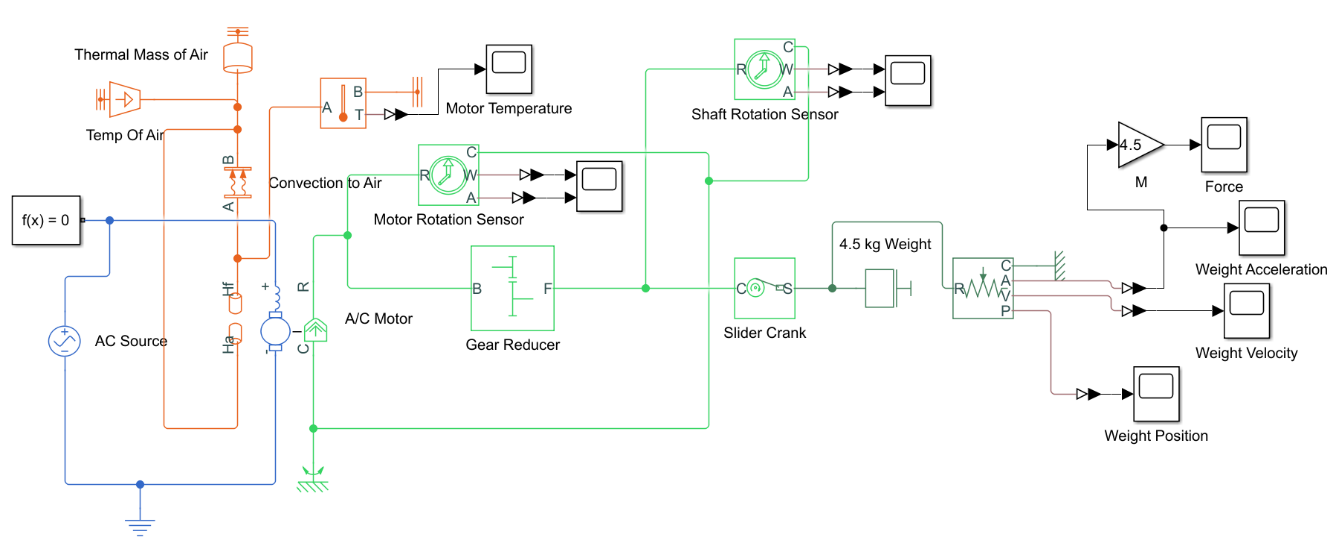
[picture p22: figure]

Figure 3: Simulink Model Diagram for Drive Train System

The blue portion of Figure 3 represents electrical supply of 230 V of AC voltage to the motor, and the motor itself is defined with specifications depicted on the motor, and from the manufacturer’s website [1]. The light green portion of Figure 3 deals with the rotational portion of the motor, including the gear reduction of 0.5, where the driver hear is twice the size of the driven gear, and a slider-crank which converts rotational motion to translational that is represented in dark green. The translational motion segment has a defined mass of 4.5 kg and ideal translational sensors to track the position, velocity, and acceleration of the weight given a user defined time. This system assumes the AC motor starts at rest. The orange portion of the figure represents thermal effects which are not relevant to this failure mode analysis.

Failure Mode #3: Overheating of the Motor

To determine the temperature effects of the motor in the system, the Simulink model was used via thermal ports built into the Universal Motor interface. The system is open to its surroundings; therefore, the thermal mass of the surrounding air is assumed to be a very large quantity. For the sake of the model, 1,000,000 kg of air was used. The temperature is assumed to on the more extreme end of weather conditions, being 90 ℉ , or 305.372 K, and the specific heat of air was input into the system, 1 J/(kg⋅K) . Finally, the main source of heat transfer in the system is convection to the surrounding air, and the governing equations which dictate this are shown below [4].

q=h⋅A⋅(T_s -T_(∞) ) (Eq. 11)

Table 5: Definition of Variables for Heat Transfer Equation

Variable symbol | Variable name/description | Variable units
q | Convection heat transfer | W
h | Heat transfer coefficient | W/(m^2 ⋅K)
A | Surface area in contact with air | m^2
T_s | Surface temperature of motor | K
T_(∞) | Temperature of surrounding air | K

While most of these variables are quite easy to estimate, one which poses a particular challenge to obtain is the heat transfer coefficient, h . This is due to the fact it is dependent on a multitude of factors, such as turbulent and laminar air flow conditions, thermal conductivity of the material, etc. For this project, conditions will vary in application, and the heat transfer coefficient is defined based on the flow of surrounding fluid being consistent, which in our case it is not. For the worst-case scenario, the heat transfer coefficient is assumed to be 5 W/(m^2 ⋅K) , which, given the high thermal conductivity of the motor's metal body, is an appropriate approximation. The area of heat transfer is assumed to be 0.25 m^2 . The thermal effects can be seen below in Figure 4.

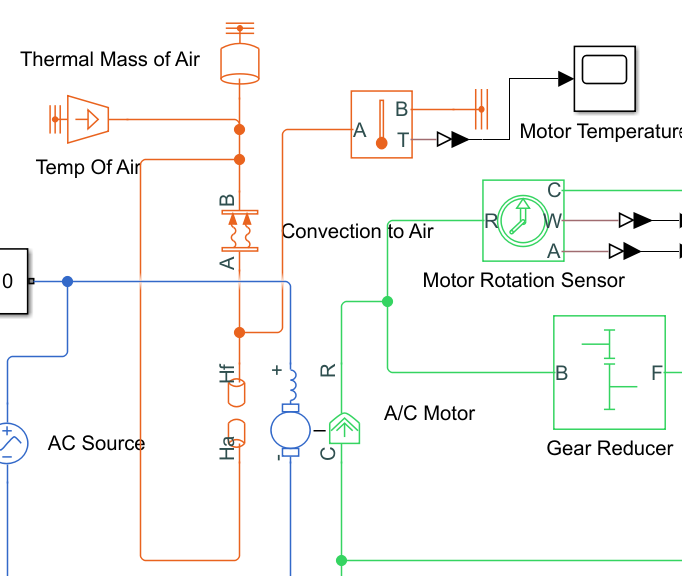
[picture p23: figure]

Figure 4: Thermal effects on the motor

This orange portion model shows the heat transfer of the motor, with it receiving and giving off heat to its surroundings. The temperature of the surface of the motor is monitored using an ideal temperature sensor.

3. Modeling/Analysis Results:

Failure Mode #1: Stress Max: 17.91 MPa, Displacement Max: 0.9643 mm, Safety Factor Min: 1.675

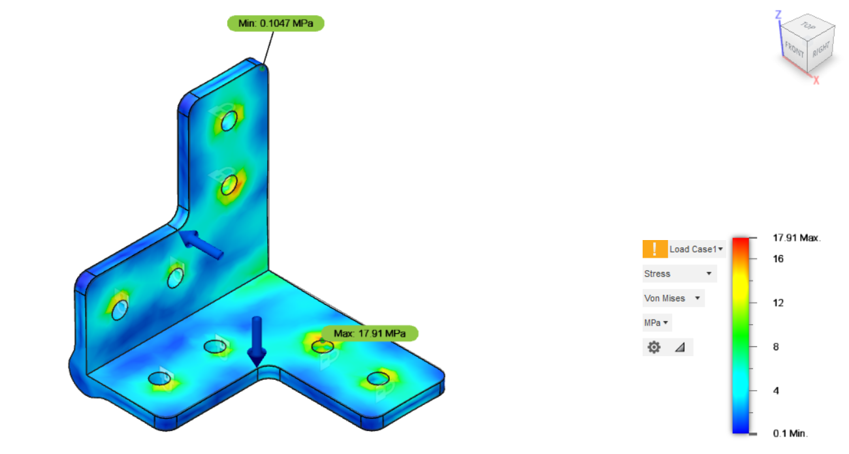
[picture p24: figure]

Figure 2: Stress simulation results.

The first modeling results analyzed were the stresses in the bracket. These results show promising signs as the maximum stress induced on the part was approximately 17.91 MPa. The National Library of Medicine says that the yield strength for polylactic acid, 3D printing plastic, is 60 MPa [5]. The bracket is well within the safe zone of this material and should be suitable for frame support. The stress maximums were located around the screw holes which was as expected.

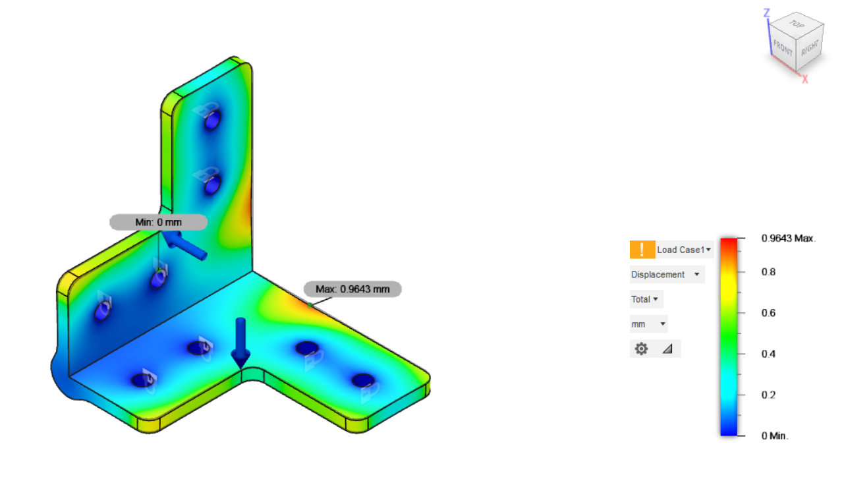
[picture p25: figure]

Figure 3: Displacement simulation results.

The second model analyzed was the displacement model for the material. This model indicates that the material will yield 0.9643 mm for the 3000 N force that will be applied. This minimal displacement will take place at two locations. Both locations are on the top of the bracket furthest away from a locked constraint or another support, which was expected. After printing and attaching the bracket to the frame, it was decided for stability purposes that an additional L-bracket should be added to the inside of the frame as to resist the flexure of the unsecured sides of the extruded aluminum.

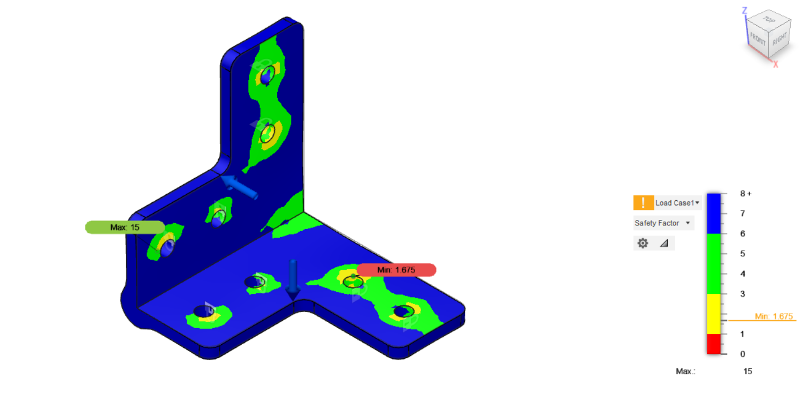
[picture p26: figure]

Figure 4: Safety Factor simulation results.

Lastly, for this failure mode, the final area explored was the safety factor of the bracket. The lowest safety factor takes place near the edge of the screw hole closest to where the maximum displacement takes place and where the maximum stress is located. With a safety factor of 1.675 the design is considered mildly safe but should have more material added to help better protect against failure. For these reasons, this area will be watched during testing. The safety factor for this area will increase with the latest adaptation to the design, which is to make was to add rectangular guiding pieces along the same axis as the screw holes. This will allow the bracket to fit snugly in the extruded aluminum pieces and mechanically join the two pieces together more adequately. From the modeling performed on the brackets, the group was able to determine that the brackets should not fail. They have a safety factor above 1 and are expected to increase further, experience stress well below the yield stress, and have a displacement of less than a millimeter. For these reasons the group has decided to move forward with 3D printing the brackets for the frame connections.

Failure Mode #2:

Input: 230 V; 100 seconds


Figure 8: Acceleration of weight for 100 seconds.

Input: 230 V; 20 seconds


Figure 9: Acceleration results for 20 seconds.

As seen in the results above in Figure 8, the acceleration when the motor reaches a steady state reaches well above 1500 m/(s^2) , which would output a force of well over 6,000 N, assuming a mass weight of 4.5 kg. The positive and negative values represent the acceleration of the weight moving upward and downward. The downward acceleration is higher due to effects of gravity. Models are not perfect, and reaching this amount of acceleration could output forces well over the amount the frame could stand before failing. Therefore, it is necessary that the motor is throttled back to the design specifications to reach the amount of force necessary for observation in the vibration analysis. The assumptions and imperfections of the model will also make this level of acceleration highly optimistic to reach. However, the acceleration of the weight reaching such high values is useful for this project, as it can be inferred that the shaker will at least be able to reach this project’s target value of 500 N.

Failure Mode #3:

Input: 230 V; 1,000 seconds; 305.372 K Air Temperature


Figure 10: Temperature of the motor in operation for 1000 seconds, exposed to 90 ℉ .

As shown in Figure 10, the motor is subjected to 105.372 K or 90 ℉ heat through operation. The temperature of the motor rises and levels off at steady state without reaching extreme temperatures, as the maximum temperature reached is less than 316 K, or 109.13 ℉ . This is well within safe operating temperatures for AC motors, and no active cooling is necessary to provide additional heat transfer. This simulation is also performed for 1,000 seconds, which is much higher than the expected time the shaker will be in use to collect data.

4. Conclusion and/or recommendations:

In this report, the first analysis performed was a simulation of the stress on the bracketing assemblies in Fusion 360 to test the strength of 3D printed brackets, which were requested by our project sponsor for their cost effectiveness. The main concern of these brackets was whether the plastic could handle the shear and bending stress, and the test was done using equations for the textbook “Machine Elements in Mechanical Design.” Based on the analysis done, the brackets should not fail, indicating that the brackets are adequate as is. The second analysis consisted of a SIMULINK model run through MATLAB to determine the output force of the motor. The results showed that the motor reaches an acceleration above 1500 m/s^2, which translates to a force of over 6,000 N with a mass weight of 4.5 kg. The downward acceleration is higher because of gravity. The high level of acceleration could result in forces beyond what the frame can handle, so the motor must be adjusted to the design specifications for the vibration analysis. The results are optimistic, but the acceleration of the weight still demonstrates the shaker’s ability to reach the target value of 500 N for this project. Based on the model, the motor is adequate and will not need to be replaced. Our third analysis was a SIMULINK model to determine the effects of the temperature of the motor during use. In the model, the motor reached a temperature of 105.372 K during operation. The temperature rises to 316 K, but it does not exceed it. That is within the safe operating range for this motor, so no additional cooling is needed. The model indicates that the temperature of the motor will not cause it to need to be replaced.

5. References

[1] Lafert HE90LE4 AC Motor 3PH 2HP 1735rpm 230/460V-AC. Surplus and Used Industrial Parts and Equipment. (n.d.). Retrieved February 6, 2023, from https://www.nriparts.com/products/lafert-he90le4-ac-motors/476553

[2] Vedantu. (2022, November 29). Relation between torque and moment of inertia. VEDANTU. Retrieved February 6, 2023, from https://www.vedantu.com/physics/relation-between-torque-and-moment-of-inertia

[3] Admin. (2022, October 20). Gear train : Gear ratio, torque and speed calculations. SMLease Design. Retrieved February 6, 2023, from https://www.smlease.com/entries/mechanism/gear-train-gear-ratio-torque-and-speed-calculation/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,Gear%20Ratio%20and%20Torque,input%20torque%20with%20gear%20ratio.

[4] Bergman, T. L., Lavine, A. S., Incropera, F. P., & Dewitt, D. P. (2016). Fundamentals of heat and mass transfer. John Wiley.

[5] Travieso-Rodriguez, J. A., Jerez-Mesa, R., Llumà, J., Traver-Ramos, O., Gomez-Gras, G., & Roa Rovira, J. J. (2019, November 22). Mechanical properties of 3D-printing polylactic acid parts subjected to bending stress and fatigue testing. Materials (Basel, Switzerland). Retrieved February 6, 2023, from https://www.ncbi.nlm.nih.gov/pmc/articles/PMC6926899/

Downey1Engineering Analysis Report02/06/2023

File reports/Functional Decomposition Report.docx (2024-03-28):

Functional Decomposition and Concept Generation

1. Introduction

Functional decomposition and concept generation is an important way of determining what a product will do and how it will accomplish it. A variety of ideas were put together in a group setting on what the functions of a finished product would be. Then, the group brainstormed ideas on how to complete each function. Finally, the group created 5 concepts for a finished product using concept ideas that would correctly complete each function.

2. Functional decomposition

Functional decomposition involves using the customer needs as a basis for determining the required functions of the product. These functions are not solutions, but rather abstract project requirements to fill with solutions later. The group brainstormed functions of the product based on the critical needs and engineering concepts previously discussed. Identified functions for the bridge shaker project in approximate order are listed below:

a. Attach to structure
b. Receive energy
c. Regulate power
d. Receive input on the desired frequency and timeframe to vibrate at
e. Determine set frequency
f. Show parameters on screen
g. Receive input to start vibration procedure
h. Convert electrical energy to mechanical energy
i. Increase or reduce frequency
j. Transfer energy to the bridge
k. Vibrate the bridge
l. Receive input to stop vibration of the bridge
m. Detach from structure

Once functions were identified, they were condensed and broken up into three categories: energy, material, and information. A functional decomposition diagram is shown in Figure 1 and is used to organize the functions and visualize interactions. The arrows identify preceding and subsequent functions depending on the head direction, and the order of functions increases from left to right. For example, receive energy precedes regulate power as indicated by the arrowhead and its position to the left of the other function blocks. As described by the functional decomposition diagram, the product must first attach to the bridge and receive electrical energy before regulating that energy and converting it into mechanical energy. That energy will be used to manipulate the frequency depending on set parameters acquired from a user. The user input will be measured and displayed after an initiation signal is received, and energy will be transferred to the bridge to induce vibration.


Figure 1: Functional decomposition diagram.

3. Concept Combinations:

The Concept Combination Table (CCT) shown in Table 1 serves to organize the possible solutions to the functional requirements of the project.

Table 1: Concept Combination Table, CCT.


With the subproblems and solutions listed out, it is easier to combine functional solutions to generate a total solution for the project. The CCT has allowed for ease of development in creating five designs for the Bridge Shaker project.

For most of the functions, the group attempted to create several solutions for the functional requirements which were broader in scope. However, for some functions, only limited solutions remained such as “Reducing/Increasing Frequency”, “Receive Power”, and “Regulate Power”. For increasing/decreasing the frequency, an Arduino or Motor Driver is the best option, as other solutions would be either overly complex or expensive. The “Receive Power” function in the CCT has so few solutions because there are not many ways to solve this apart from the most convenient options such as wall outlets, generators, and batteries. A similar thought process guided the creation of the “Regulate Power” function of which the Power Management Integrated Circuit (PMIC), microcontroller, or Metal Oxide Semiconductor Field Effect Transistor (MOSFET) seemed to be the most viable options. The other functions with more solutions have some with greatly desired methods and some that are not. For instance, attaching the bridge shaker via epoxy would be greatly undesired due to the difficulties inherent in working with epoxies such as the mess and effort in application. Other solutions seem to be no-brainers in their use, but there are some solutions where choosing the best option is not as simple. For instance, the method to convert electrical energy to mechanical energy has several options. The motor with an offset or linear weight and solenoids could both be great methods, but the choice will influence the remaining solutions of other functions like “Receiving Power”.

4. Concept Generation:

Five concepts were generated using the Concept Combination Table. A basic schematic and description of each concept was developed by the group. The following concepts were developed.

Table 2: Concept Generation; Concept 1.


Concept 1: A motor is powered by a wall outlet with power regulated by a microcontroller. The motor rotates an asymmetric offset weight to induce vibration by converting electrical energy into mechanical energy. User input on frequency and test time is gathered through buttons read through a microcontroller, which increases or decreases the frequency by altering the power. Energy is transferred to the bridge with a shaker weight. The shaker is attached and released from the bridge using clamps to the sides of the bridge.


Figure 2: Concept sketch 1.

Table 3: Concept Generation; Concept 2.


Concept 2: The power from the battery is put through a PMIC and goes to an Arduino. The Arduino takes keypad entries from the user to control the speed of the solenoids which impact the platform and induce vibrations in the bridge. The apparatus is connected to the bridge with bolts, and energy is transferred to the bridge through this connection.

Figure 3: Concept sketch 2.


Table 4: Concept Generation; Concept 3.


Concept 3: A motor is powered by a separate generator. The voltage from the generator is regulated via a MOSFET. The DC Motor turns a pulley that draws the weight upward towards the top of the frame. Then, by control of the microprocessor, when given an input from the remote control, the device will drop the weight and pick it back up repeatedly until instructed to stop. The entire apparatus will be held down by rachet straps connected to the bridge and the mode of energy transportation will be via the counterweight.


Figure 4: Concept sketch 3.

Table 5: Concept Generation; Concept 4.


Concept 4: A wall outlet supplies power which is regulated by a microcontroller to an air compressor. This compressor powers a hydraulic actuator with a large surface area on the end to strike the bridge to induce vibration. The user inputs frequency and testing time via a touchscreen, which is read by an Arduino to increase or decrease the frequency by controlling the air compressor. The system is secured by ratchet straps, and energy is transferred to the bridge from the weight of the system.


Figure 5: Concept sketch 4.

Table 6: Concept Generation; Concept 5.


Concept 5: A generator is regulated by a MOSFET and powers a motor with a linear weight. The motor is controlled by an Arduino which takes input from a keypad. The device is encased to protect the parts and the whole device is tied down with rachet straps. The energy is being transferred to the bridge through the linear weight being driven up and down by the motor and links.


Figure 6: Concept sketch 5.

5. Research performed

The keywords “mass shaker”, “structures”, and “test” into the Google Patent search engine revealed some relevant patents that were useful in illuminating methods of inducing vibrations. Patent EP2589947B1 [1] presents a high-frequency vibration system that uses the piezoelectric effect to induce vibration through a disk-shaped contact structure that the object sits upon. Patent SU325770A1 [2] was found that depicts a pneumatic vibrating device. This device uses compressed air alternately pushed into opposite sides of the cylinder creating a vibration. This patent resembles the hydraulic piston concept generated in the above section. Patent EP0566809A1 [3] shows a fruit harvester that clamps onto a tree trunk and uses linear impact vibrations to shake fruit off the branches. Its primary method of vibration inducement is motors with offset weights which are connected to an excitation rod attached to the tree trunk by a clamp, and the vibrations transmitted through the rod and the impacts acting on the tree cause the fruit to fall.

6. Conclusion

Concept generation can be a difficult task. Prior to concept generation, the functions of the device were laid out sequentially to give the team an idea of the technologies needed for each step. Next, the concept combination table was created to brainstorm ideas that could fulfill each function. Lastly, from this table concepts were generated that will satisfy all stakeholders. In doing so, some technologies were found to be unrealistic, or would not necessarily suit the needs of the sponsor. An example of this was the use of hydraulic pistons to convert electrical energy into mechanical energy. Discussion led to the conclusion that the pistons would not be able to alternate fast enough to produce the vibrations desired and that the fluid inside of the pistons would dampen the vibrations. On the other hand, it was determined that the DC motor, in combination with either linear weight oscillation or offset weight, would be the most likely conceptual design for any scenario. This keeps the design comparatively simple and easily controllable by the user. Even though the device will be simple, it will still be difficult to design the shaker to oscillate the bridge at the desired frequency. In another interview with stakeholder Joud Satme, he expressed concerns about the functionality of single-frequency excitement. This conversation led to the development of Design Five. The next step will be to evaluate the concepts after discussing them with the sponsor, Dr. Austin Downey, and ultimately selecting a design to move forward with.

References

[1] James P. Rogers, Abbas Mandvi, Chi Chin LEE, Chhour M Thong, Anthony Charles Buono, “High frequency vibration system”, European Patent 2589947B1, Feb. 12, 2020.

## [2] Н. А. Клушин, В. Н. Шмигальский, П. А. Маслаков, Э. П. Варнелло, Э. А. Абраменков “Pneumatic Vibrator”, Russian Patent SU325770A1.

[3] Domingos P. Sousa, Pedro J. Oliveira, “Improvements in the mechanical shaker for fruit harvesting”, European Patent 0566809A1, Oct. 27, 1993.

Downey1Concept Generation10/24/22

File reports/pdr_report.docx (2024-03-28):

Preliminary Design Review Report

1. Brief Background

The team was tasked with creating a long-term usable product by the Adaptive Real-Time Systems (ARTS) Laboratory. Dr. Austin R.J. Downey is the head of the laboratory and the studies that it conducts. The ARTS Lab is developing a sensor package to measure vibrations in bridges; therefore, a shaker is needed to excite the bridge to determine mode shapes. The current shakers in the ARTS Lab are too small to excite large structures hence the need for a more powerful shaker. Impulse testing has been performed on bridges, but continuous testing is desired. Continuous testing allows for testing different frequencies and permits excitement to more modes. Our purpose as the design team is to create a shaker for continuous bridge vibration testing so that the ARTS Lab can use this shaker for more accurate data acquisition in the sensor packages. Throughout the semester, the team had to objectively identify customer needs, project specifications, and product functionality, design viable shakers for continuous testing of vibration data, and next semester the team must build and test a final design for the shaker to deliver to the ARTS Lab.

2. Customer Needs and Requirements

After meeting with Dr. Austin Downey, the project sponsor, a comprehensive list of needs was made to include what the final design should have. The list created for this project is shown below.

Table 1: List of preliminary needs.


After voting on all 36 original needs, the top seven moved on to the second round of voting to determine the critical to quality (CTQ) needs. These top needs are shown in table 2 below.

Table 2: List of priority needs.


This voting process allowed the group to view the project from the perspective of abundant needs as well as a simpler, more concise list of needs. From the voting process outlined in the two tables above, a product mission statement was created from the top four needs and shown below.

“Dr. Austin Downey needs a bridge shaker that needs to test vibration data, operate at different frequencies, be safe to operate, and leave the bridge undamaged.”

3. Key Engineering Characteristics/Specs

Below is a quality matrix showcasing all the engineering characteristics of the project. The engineering characteristics (EC’s) are shown as the columns and the rows are customer requirements. Each EC was given numeric values of 1, 3, or 9 to indicate how strongly it contributes to the customer requirement. A 1 indicates low correlation while 9 indicates high correlation and leaving the cell blank indicates no correlation.

Table 3: Quality matrix showcasing engineering characteristics.


List of Critical EC’s:

- Adaptability
- Usability by others
- Product details

From the quality matrix, the critical EC’s are determined to be adaptability, usability by others, and product details. Adaptability would be an important characteristic of the project as the bridge shaker would need to be able to excite more than one bridge. Usability by others was important because researchers should be able to use the shaker without much difficulty. The last critical EC, product details, was important because good documentation helps ease of use, adaptability, and other engineering characteristics become more doable.

4. Selected Concept


Figure 1: Side view of design will all components visible.


Figure 2: Two side views with labeled parts.

This updated design has some notable updates including the following in Figures 1 and 2:

- Inverted the gear ratio to favor speed over torque, therefore needing to raise the motor on a platform.
- The MOSFET has been replaced with a motor driver, which will directly control the speed of the motor with the voltage control on the analog dial.
- The frequency will be determined based on the tachometer which will be attached to the sheave to observe the rotation rate. This information will be shown on the LCD screen with the aid of an Arduino.
- The motor driver will plug directly into a wall outlet, which will facilitate the need for an extension cord.

Strengths:

- Compact design.
- Easy analog control of motor.
- Very high output force according to simulations run on Simulink, as well as easier to simulate as opposed to the other designs.
- Relatively simple and intuitive design, low maintenance with the use of a belt.
- Very economical and cost-effective compared to other designs considered.

Weaknesses:

- No feedback control to get a specific frequency and will have to tune it manually.
- The maximum output force could shake components loose or worse, destroy the product. Precautions and perhaps limiting the maximum voltage output of the motor driver could be necessary for safety and longevity purposes.
- The friction between the weight and its sleeve will need planar joints and possible lubricants to keep down wear and tear, as well as minimize heat.
- Moving parts pose a safety hazard that can be mitigated with barriers.
5. Architecture


Figure 3: Product layout with functional clusters.

The functional components have been divided into five clusters as seen in Figure 3.

1. The first cluster is the attach/detach cluster which only contains the ratchet straps, which are used to secure the shaker to the bridge.
2. The second cluster is the power supply, which consists of the wall outlet to supply electrical energy to the system.
3. The third cluster is frequency regulation, which houses the motor driver which takes an analog input from the user for power regulation, which in turn will regulate the frequency/speed of the motor.
4. The frequency regulation cluster directly impacts the vibration mechanism, as the motor driver will change the speed of the motor, thus changing the linear velocity of the weight via the gear train.
5. The vibration mechanism cluster will directly affect the user interface cluster by having a tachometer attached to the sheave. This will be displayed on the user interface via an Arduino and LCD to show the current frequency of the sheave with the weight.

Some consequential interactions are as follows:

1. The vibrations from the shaker will be transferred to the electronics and the shaker frame. To minimize this effect, each element will be secured to the frame to minimize any extra shaking of components.
2. Heat will be generated from the motor as well, which may decrease the longevity of the shaker. The effect of heat generation could be lowered by allowing adequate airflow.
3. The shaker presents a possible safety hazard to any user as it has many moving parts and will have a moving weight. To fix this problem, steps can be taken to make the shaker more user-friendly such as adding handles for a better grip or covering dangerous moving parts.

The approximate dimensions of the shaker are 2 ft by 2 ft for the portion touching the ground and around 2.5 ft tall, as seen in Figures 1 and 2. This should supply adequate room for all the moving parts. The largest gear will be a foot in diameter, and the other two which will be attached via a belt to the large gear and linkage to the weight will both be four inches in diameter. The linkage will be 6 inches long, and the 5 kg weight itself, assuming being made of 3003 Aluminum, will be 4 inches in diameter and 7.874 inches in height.

6. Identification of critical decisions TBD

Key critical decisions that are yet to be determined are as follows:

- Frequency range: the realistic frequency range of the shaker must be customized for the bridges that it will be tested on. Current values are estimates based on past work and input from stakeholders, but the team will perform testing on the bridges using accelerometers to determine the frequency requirements of the shaker. This testing will be conducted in late December/early January.
- Motor: this is the motor that will turn the gear train to oscillate the weight at the desired frequency. This is still a TBD because the ARTS Lab already has a motor that may be used for the shaker, but testing must be done to determine if the maximum rpm is sufficient to reach the highest required frequency. This will be determined once the first prototype of the shaker is built in late January.
- Types of bearings: these bearings will be implemented to control the movement of the weight and constrain its pathway. This is still a TBD because the team lacks technical knowledge on the bearings required to support the highest frequency of the weight. This TBD will be resolved once the maximum frequency of the weight is determined in early January.
7. Preliminary Budget

Preliminary budgets were created in triplicate to show the variety of materials available to complete the shaker. Items were sourced from different websites and distributors to determine the best parts to take and implement into the groups design. Table 1 houses all this information and shows the prices for each component identified. At the end of each bill of materials, there are two values listed. The first is the subtotal which is just the raw price of the components added together. The total amount considers an extra 25% in value to cover shipping, contingencies, taxes, etc.

Table 4: Bill of Materials, completed in triplicate.

Each corresponding bill of materials has similarly high value items. This is the motor, the v-belt sheaves, and the frame for the shaker to sit in. these items will need to be reviewed in depth to weigh the pros and cons for purchasing. These items also must be purchased first because they likely have the largest lead time and will be the major source of change if something were to go wrong. Lastly, the only ‘to be determined’ item is the bearings. The bearings will need to be designed to fit the shafts purchased and the supports created. There is also further discussion to be had about the types of bearings needed for this design. Bearings should be sourced by the end of December.

8. Future work

The tentative timeline for the bridge shaker project is shown in Table 5. The team will spend most of its time validating and refining the first prototype in order to deliver an excellent end product.

Table 5. Proposed timeline for bridge shaker project.

| Jan | Feb | Mar | Apr | May
Accelerometer testing | X
Engineering analysis | X | X
First prototype construction | X | X
Validation and refinement | | X | X | X
Final product construction | | | | X
Product and documentation delivered | | | | | X

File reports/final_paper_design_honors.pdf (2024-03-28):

BRIDGE SHAKER

By

### Corinne Smith, Alexander Toth, Ryan Yount, Ryan Brown

### Submitted in Partial Fulfillment of the Requirements for Graduation with Honors from the South Carolina Honors College

### May 2023

### Approved:

### Dr. Andrew Sabalowsky Director of Thesis

### Steve Lynn, Dean For South Carolina Honors College

## Table of Contents

## A. Preface

A.1. Executive Summary

The Adaptive Real-Time Systems (ARTS) Lab is a research lab that develops sensor packages for

structural health monitoring. They want a product that continuously excites different structures to permit

continuous time testing of bridges to validate their vibration sensor packages.

Needs of the ARTS Lab were determined by identifying and independently ranking a list of needs, and

after detailed analysis, it was determined that testing vibration data, operating at different frequencies, being

safe to operate, and leaving the bridge undamaged were critical to satisfying those needs. It was furthermore

determined that a product to satisfy their requirements would need to test vibration data and be usable by

future researchers. It was thus determined that the product mission should be to create a bridge shaker that

needs to test vibration data, operate at different frequencies, be safe to operate, and leave the bridge

undamaged.

Given the above requirements, multiple concepts were researched and considered, as described in this

report. The ultimate concept selected to best satisfy the ARTS Lab’s needs was excitation via an AC motor

and gear train for linear actuation. Details related to concept selection and subsequent product architecture

are supplied.

The bracket stress, output force, and motor temperature are critical to functionality, and detailed

engineering analyses are provided, demonstrating how bracket stress, output force, and motor temperature

were modeled, under conditions of high frequency operation, and the design was optimized for a maximum

bracket stress of 17.91 MPa, a maximum force output of 6000 N, and a maximum motor temperature of

316K. As a result, the system was able to output more than enough energy to excite the structure and stay

within safe operating temperatures, though some of the 3D brackets experienced failure along the layer

lines, which could not have been simulated and predicted in Fusion 360.

Because parameters safety, durability, and ease of use are high priorities for production of the product,

the design was optimized for these parameters as well, which consisted of adding additional weight to

secure the shaker, sourcing high quality materials, and making the project entirely open source.

The prototype was tested by measuring vibration output accuracy, testing the shaker’s operation at a

wide range of frequencies, operating the shaker at small step sizes and comparing the bridge response,

weighing the shaker, inspecting any failed components after high frequency testing, and measuring the

displacement of the shaker before and after operation. These tests were performed outdoors in 60-80 degree

Fahrenheit weather on a pedestrian bridge with a high stiffness value.

Economic analysis of the scope of expenses associated with development of the prototype indicate that,

for a $4,736 investment, the ARTS Lab will recover costs within 7.7 years if they chose to sell units rather

than earn profit from research grants.

The bridge shaker presented in this work meets the majority of the customer needs and product

specifications, falling short on robustness and bridge contact. Robustness is increased by substituting higher

quality brackets and bearings into the design, and bridge contact is improved through adding additional

weight to the shaker during high frequency operation. Both issues have been addressed and require further

formal testing to validate the design changes.

A.2. Background

The Adaptive Real-Time Systems Lab is a research lab at the University of South Carolina under Dr.

Austin R.J. Downey. One specialization of the ARTS Lab is unmanned aerial vehicle deployable sensor

packages for structural health monitoring. The lab has developed a sensor package to measure vibrations in

bridges. A challenge the lab is facing is being able to perform continuous time testing of vibrations in

bridges, as they would need a modal shaker to excite the bridge for minutes at a time. The lab can perform

impulse testing, which involves striking the bridge just once to measure the decay signal, but there is a need for continuous time testing to further the lab’s research on structural health monitoring applications of its

sensor package.

The purpose of this project is to design and develop a bridge shaker that will provide the lab with an

instrument to perform continuous time testing with its vibration sensor package. The shaker is intended to

be used by the lab for expanding the type of testing they can perform, which will further their research and

entice new grants.

## B. Customer Needs

B.1. Introduction The goal of this project is to create a bridge shaker that, when placed on a bridge, excites

multiple frequencies and modes within that bridge. Dr. Austin Downey wishes this device to test

a wide variety of bridges and gather information on the structural integrity and health of the bridge.

The purpose of this chapter wasto begin the design process by determining and ranking the sponsor

needs. The conceptualized needs were listed and defined in relation to the scope of the project.

They then underwent two rounds of independent ranking in order to identify which were the

highest priority needs. Finally, the project mission statement was formed based on the critical

needs.

B.2. Interpretation of Needs This section outlines the 36 needs that were brainstormed by the design team and defines

each need to promote clarity.

1. Needs to be used to test vibration data – the bridge shaker must be able to shake the bridge
| being tested at a high enough frequency to match our control data.
2. Needs to ideally excite the fourth or fifth mode – the shaker needs to be able to shake the
| bridge well enough that the fourth and fifth mode can be seen on an FFT diagram.
3. Needs to have a max range based on experimental data gathered by accelerometers – testing
| data from normal bridge activity must be recorded to create a baseline for the shaker to operate
at.
4. Needs to be robust – the design of the shaker needs to be simple and easy to put together,
| must not be too complex.
5. Needs to be usable in the future – the shaker needs to remain a useful tool for future
| experiments even after the conclusion of this project.
6. Needs to be site flexible – it must be applicable to a multitude of different bridge sizes and
| dimensions; needs to be simple enough for a wide range of applications.
7. Needs to be portable – by making the shaker light and easy to carry, the shaker is able to
| be used in a variety of different locations.

8. Needs to be user friendly – the controls and functionality of the shaker need to be simple enough so that someone with a little experience can operate the machine.
9. Needs to run off a portable power supply – some bridges may not have an outlet nearby for us to supply power to the shaker, therefore it will need some sort of internal power system.
10. Needs to tell the frequency it is operating at – a display for the current frequency the shaker is operating at so the value can be checked with a control test.
11. Needs to have feedback control – it needs feedback control on the responsiveness of the shaker and operating parameters; needs to be easily adaptable.
12. Needs to have a screen to monitor parameters – some sort of LCD needs to be incorporated to keep track of operating parameters.
13. Needs to transfer energy to bridge – a good connection to the bridge is required so that the energy of the shaker is transferred into the bridge and not dissipated elsewhere.
14. Needs to have high efficiency – must create minimal losses from the shaker itself or any other factors; needs to exert an equal value of energy to that it is using.
15. Needs to have good contact to bridge – needs good contact to the bridge so that the shaker will not tear itself apart or damage the bridge.
16. Needs to leave the bridge undamaged – the bridge's integrity needs to be upheld in an equal condition to which it started.
17. Needs to be minimally invasive – these bridges are community bridges, so the shaker and accelerometers need to be as convenient as possible for all foot traffic pedestrians.
18. Needs to be small enough to not affect vibration data – the size of the shaker needs to be small enough and light enough so that it does not dampen the vibrations in the bridge.
19. Need accelerometers to capture very high/low frequencies for validation – a wide range of frequencies must be accommodated in the design parameters.
20. Needs user controllable speed – the shaker must have some sort of controllable speed input to control the frequencies being created.
21. Needs to be replicable by other researchers – the shaker must be simple enough so that others interested in this work are able to recreate the design.
22. Needs to be easily repairable – the shaker must be easily repairable. Since the shaker is under continuous stress, anything that fails must be easily fixed.
23. Needs to be cost-effective – the shaker must not be extremely expensive, and the operating costs need to be low as well.
24. Needs to withstand the stress of operation – no matter the design, the shaker needs to produce extreme forces to create vibrations, therefore it must withstand its own energy output.
25. Needs to record data - accelerometer placement needs to be strategic to record the best and most useful data.
26. Needs to be aesthetically pleasing – since the experiments take place in public, the shaker must not be threatening-looking.

27. Needs to operate at different frequencies – frequency design parameters need to be set to ensure the shaker can operate in a full range of frequency.
28. Needs a resolution of at least 1 Hz – the shaker must be programmable within a 1 Hz resolution.
29. Needs to be power efficient – needs to output as much energy as it is taking in, ease of energy calculations.
30. Needs to be validated with data at different times of day – vibration data across the bridge in a normal day's time needs to be recorded to find the full range of vibrations experienced by the bridge.
31. Needs to operate at a variety of temperatures – the effect of temperature on the performance of the bridge is also of interest so the shaker needs to operate in extreme heat and cold.
32. Needs to be well documented (GitHub repository) - all data and documents need to be stored so that the public can see and recreate our experiment.
33. Needs to have clear operation instructions – the shaker must have instructions that allow someone with little experience to operate the shaker effectively.
34. Needs to be safe to operate – the shaker will operate in a public space; therefore, it needs to be safety tested before it is introduced into the public environment.
35. Needs to have a failsafe – a safety switch must be installed for an automatic stopping system.
36. Needs to have time control – the testing will take place over extended periods of time; therefore, it will need a timer to operate on.

B.3. | Affinity Diagram
| Round 1 consisted of 50 points per person voting on all 38 needs and is shown in Table

B1. For the first round, each need was independently given a score pulled from the 50 points based

on how important it appeared to be. More points indicate a more critical need. The total points for

each need were added up and the top seven needs were identified to move forward in a second

round of voting. The top seven needs were chosen because they represent the 80th percentile of

the 36 needs.

Table B1. First round of needs ranking

The top seven needs from round 1 moved on to round 2, shown in Table B2, where they

were ranked from highest priority to lowest, with 1 as the highest priority and 7 as the lowest. The

voting was conducted similarly to the first round, but each team member had only 28 points to

distribute in round 2. The top four from round 2 were used to form the product mission statement.

Table B2. Second round of needs ranking.

B.4. Product Mission Statement

Dr. Austin Downey needs a bridge shaker that needs to test vibration data, operate at different

frequencies, be safe to operate, and leave the bridge undamaged.

## C. Project Specifications

C.1. | Introduction
| The product specifications phase of the design process determined ways to quantify the

previously identified critical needs into specific engineering characteristics for the product. The

needs list was consolidated to eliminate redundancies and the 15 most important needs based on

the affinity diagrams in section B.3. are assigned metrics and units in the needs matrix. Engineering

characteristics are then assigned for each customer requirement and the correlation of each with

the needs is shown in the needs metrics matrix. Finally, target and fallback specifications for each

important metric are assigned. The value of this section for the design process was the

identification of critical specifications.

C.2. Needs Matrix

When deciding the needs for the bridge shaker, redundancies in the previously defined needs

were identified to create a more concise list. Fifteen out of the original 36 needs were kept. Each

need was evaluated individually to determine the importance of the characteristic for the final

product. Some needs such as site flexibility, minimal invasiveness, and small size were cut in favor

of portability as an umbrella need. Ways to validate the performance of each customer need were

brainstormed to produce metrics and their corresponding units. Each metric and unit were

collectively discussed in relation to each specific need.

The client requires an accurate way of measuring the desirable characteristics for excitation

over an extended period to test structural integrity of a bridge. This means that the shaker needs to

operate at different frequencies to recreate the modal frequencies of the bridge. This project is well

documented, with data while using the shaker being recorded, as well as a time control on the

shaker to supply timed testing. The client also recommended safety and ease of use so that researchers could comfortably use the shaker for vibration experiments. After further discussion,

the bridge shaker needs to be robust, have good contact with the bridge, and leave the bridge

undamaged. These characteristics were clear needs for the shaker to meet the purpose of a long

lasting and useful experimental tool. All the needs discussed were organized into Table C1 with

the units and metrics included.

Table C1. Needs matrix.

C.3. | Needs Metrics Matrix
| The needs metrics matrix is presented in Table C2 as a method of determining

relationship strengths between customer requirements (CRs) and engineering characteristics

(ECs), as well as determining which engineering characteristics are most significant.

Table C2. Needs metrics matrix.

After the list of needs was refined and each need translated into a CR, an importance weight

factor was assigned to each CR. This weight factor ranged from 1-5 with 5 being the most

important, and needs were ranked relative to one another. This was done as a group to consider all

factors collectively. Next, the corresponding ECs and metrics were listed along the top of the

matrix and the improvement direction of each EC was determined, which contextualized each need

relative to the entire project. After this, the ECs were divided among the team members and the

correlation of each EC with the different CRs was ranked with a 0, 1, 3, or 9 for no, low, medium,

or high correlation. The ranking was divided up here to consider each EC independently from the

other ECs and reduce group member influence on the scores, as the strength coefficients were

scored more objectively than the importance weight factors. The EC strength coefficients were

limited to 0, 1, 3, or 9 to reduce the subjectivity of the scoring method by eliminating “in-between”

scores. Once all strength coefficients had been assigned, the raw value and relative weight of each

EC was calculated and ranked to determine the most significant ECs. It was found that the most

significant ECs, which were ranked 1-3 and represent the 80th percentile, were the system’s

environmental adaptability, its usability by others, and the documentation of product specs. The

priority CRs were found to be the ability to test vibration data and the usability of the system by

future students.

C.4. | Target and Fallback Specifications
| Determining target and fallback specifications is vital to the success of the product.

Finding values or parameters that suit the sponsor's needs is time-intensive and important so that

the satisfaction of the sponsor is met. All metrics, units, target, and fallback specifications can be

found in Table C3.

Table C3. Target and fallback specifications.

For the shaker, multiple sources were found that had identical or similar experimental ideas

and setups. From these, several target and fallback specifications were determined. Some

specifications came from the direct wants of the sponsor and others came from researchers in the field. Lastly, a few came from theoretical ideas that are ingrained in the basis of engineering.

Specific reasons for why the target and fallback specifications were chosen can be found next to

the source in the References section.

C.5. Conclusions

This project focuses on the creation of a bridge shaker with the ability to excite bridges to the

target frequencies specified in table C3. The primary requirement of this project is the adaptability

of the shaker for other engineering projects. Therefore, the shaker must be well-documented and

intuitive to use by others. One of the main challenging specifications for this project is to ensure

the vibrations and forces generated by the shaker do not damage its own components. One critical

specification worth noting is to ensure the shaker produces adequate force to induce an output

range with a maximum of 20 Hz.
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

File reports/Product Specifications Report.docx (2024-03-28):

Product Specifications Report

1. Introduction:

Methods to check a bridge’s health are important in ensuring the safe transportation of vehicles and pedestrians. To assess the condition of a bridge, the response of its natural frequencies, damping, and mode shape vibration under a dynamic load must be experimentally obtained [1]. The shaker is meant to be an easy-to-use, portable, and robust instrument that gathers and displays data to the user concerning power, frequency, and energy applied. The aim of this project is to excite the bridge to certain frequencies and gather data that could aid other researchers in differing experiments which require the need for a bridge shaker. These needs and requirements are summarized below in the form of a needs matrix, needs metrics matrix, and a target and fallback specifications table.

2. Needs Matrix:

When deciding the needs for the bridge shaker, redundancies in the previously defined needs were identified by the group to create a more concise list. Fifteen out of the original 36 needs were kept. Each need was evaluated individually to determine the importance of the characteristic for the final product. Some needs such as site flexibility, minimal invasiveness, and small size were cut in favor of portability as a need. Ways to validate the performance of each customer need were brainstormed in order to come up with metrics and their corresponding units. Each metric and unit were collectively discussed in relation to each specific need.

Table 1: Needs Matrix


The client required an accurate way of measuring the desirable characteristics for excitation over an extended period to test structural integrity of a bridge. This meant that the shaker would need to operate at different frequencies to recreate the modal frequencies of the bridge. This project would ideally be well documented, with data while using the shaker being recorded, as well as a time control on the shaker to supply timed testing. The client also recommended safety and ease of use so that researchers could comfortably use the shaker for vibration experiments. After further discussion, the bridge shaker needed to be robust, have good contact with the bridge, and leave the bridge undamaged. These characteristics were clear needs for the shaker to meet the purpose of a long lasting and useful experimental tool. All the needs discussed were organized into Table 1 with the units and metrics included.

3. Needs Metrics Matrix:

Table 2: Needs metrics matrix.


The needs metrics matrix is presented in Table 2 as a method of determining relationship strengths between customer requirements (CRs) and engineering characteristics (ECs), as well as determining which engineering characteristics are most significant. After the list of needs was refined and each need translated into a CR, an importance weight factor was assigned to each CR. This weight factor ranged from 1-5 with 5 being the most important, and needs were ranked relative to one another. This was done as a group to consider all factors collectively. Next, the corresponding ECs and metrics were listed along the top of the matrix and the improvement direction of each EC was determined by the group, which contextualized each need relative to the entire project. After this, the ECs were divided among the team members and the correlation of each EC with the different CRs was ranked with a 0, 1, 3, or 9 for no, low, medium, or high correlation. The ranking is divided up here to consider each EC independently from the other ECs and reduce group member influence on the scores, as the strength coefficients could be scored more objectively than the importance weight factors. The EC strength coefficients were limited to 0, 1, 3, or 9 to reduce the subjectivity of the scoring method by eliminating “in-between” scores. Once all strength coefficients had been assigned, the raw value and relative weight of each EC was calculated and ranked to determine the most significant ECs. It was found that the most significant ECs, which are ranked 1-3 and represent the 80th percentile, are the system’s environmental adaptability, its usability by others, and the documentation of product specs. The priority CRs were found to be the ability to test vibration data and the usability of the system by future students.

4. Target and Fallback Specifications:

Table 3: Target/Fallback Specifications.


Determining target and fallback specifications is vital to the success of the product. Finding values or parameters that suit the sponsor's needs is time-intensive and important so that the satisfaction of the sponsor is met. Using previous experiments, opinions, and others' expertise to determine logical values is what produces a good product. For the shaker, multiple sources were found that had identical or similar experimental ideas and setups. From these, several target and fallback specifications were determined. Some specifications came from the direct wants of the sponsor and others came from researchers in the field. Lastly, a few came from theoretical ideas that are ingrained in the basis of engineering. Specific reasons for why the target and fallback specifications were chosen can be found next to the source in the References section. All metrics, units, target, and fallback specifications can be found in Table 3.
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

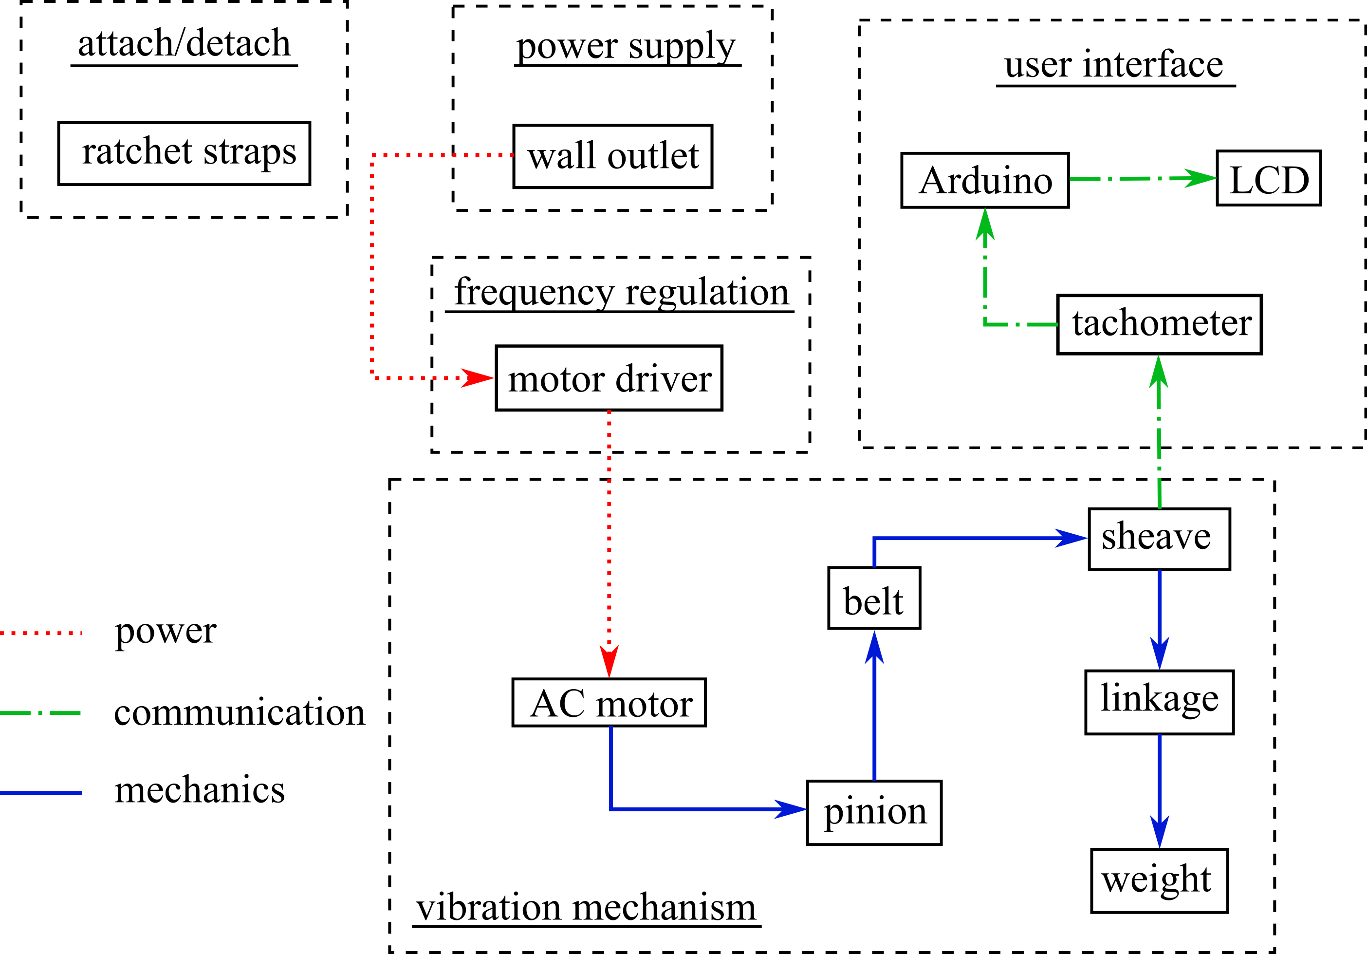
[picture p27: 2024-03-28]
images/product_architecture.png

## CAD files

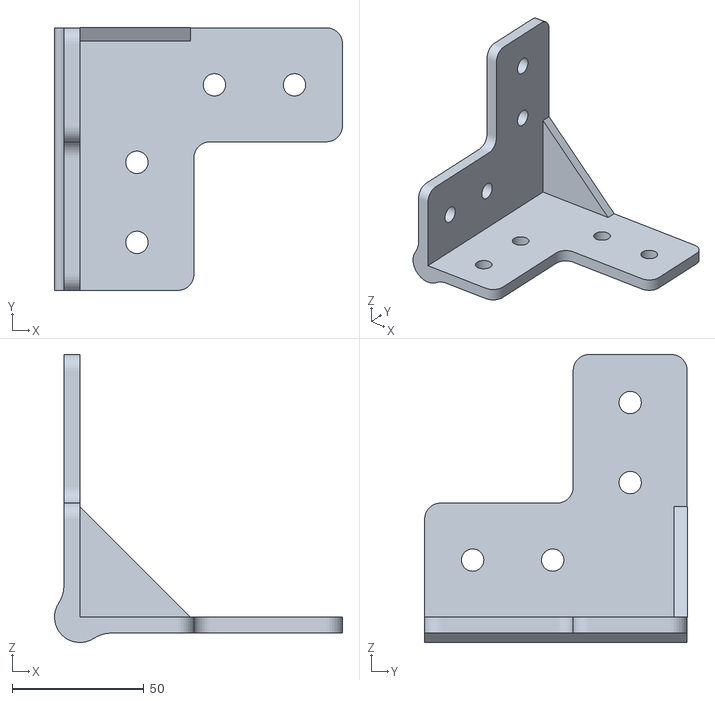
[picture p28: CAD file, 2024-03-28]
CAD files/connectors/20 Two-Way Connector v12 v6.stl
109.3 x 99.8 x 109.3

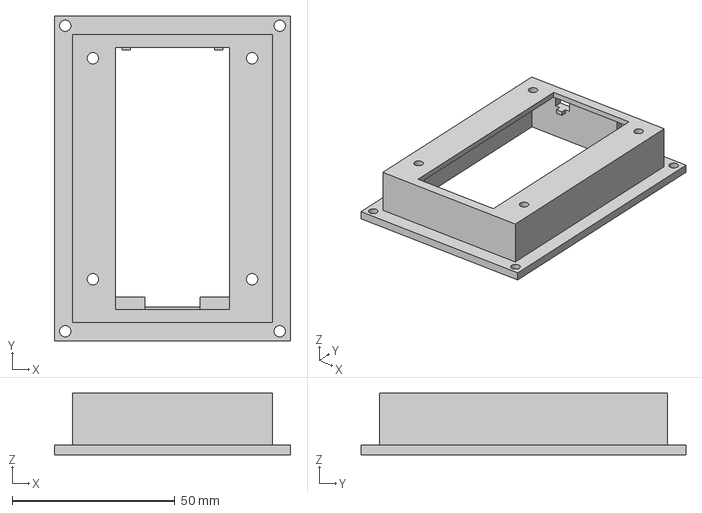
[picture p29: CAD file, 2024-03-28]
CAD files/electrical/vfd_face v4.step
72.8 x 100.0 x 19.0 mm

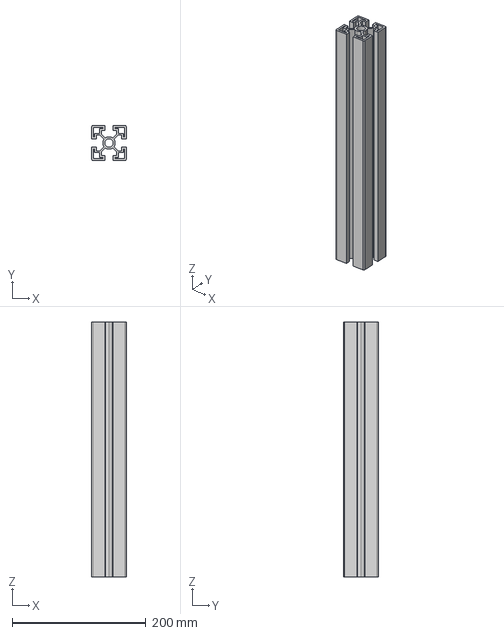
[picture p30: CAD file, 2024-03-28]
CAD files/extruded_aluminum/extruded_aluminum_15_in_f360 v1.step
52.2 x 52.5 x 381.0 mm

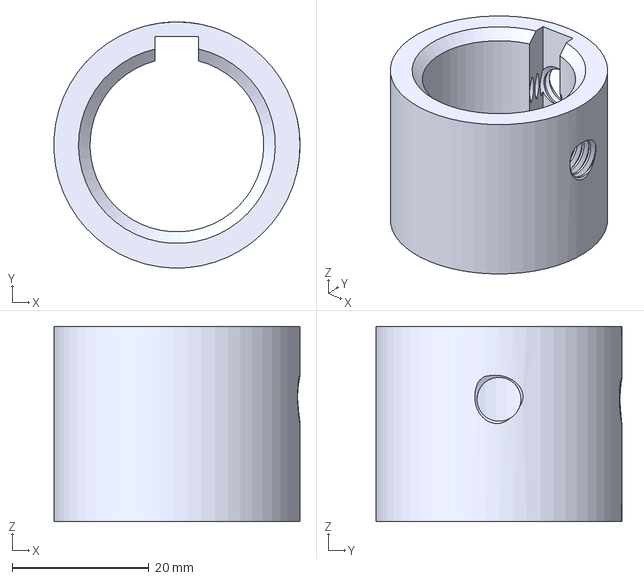
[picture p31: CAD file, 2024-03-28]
CAD files/mechanical/001_grainger_fixed_bore_94 v2.step
36.0 x 36.0 x 28.6 mm

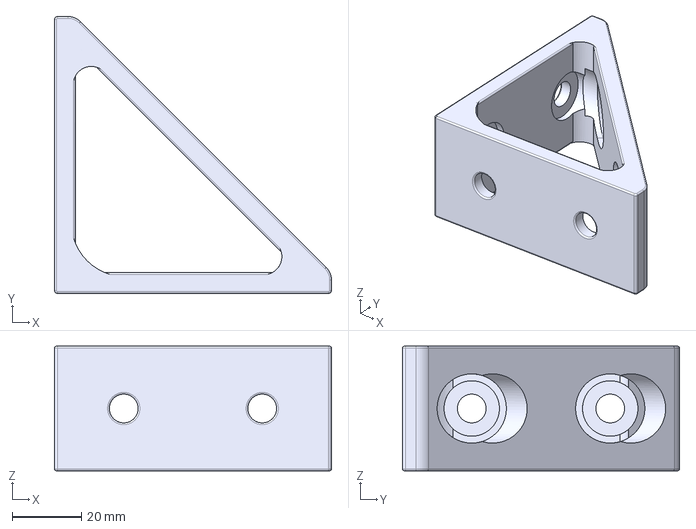
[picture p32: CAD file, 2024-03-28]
CAD files/connectors/triangle_bracket.step
80.0 x 80.0 x 36.0 mm

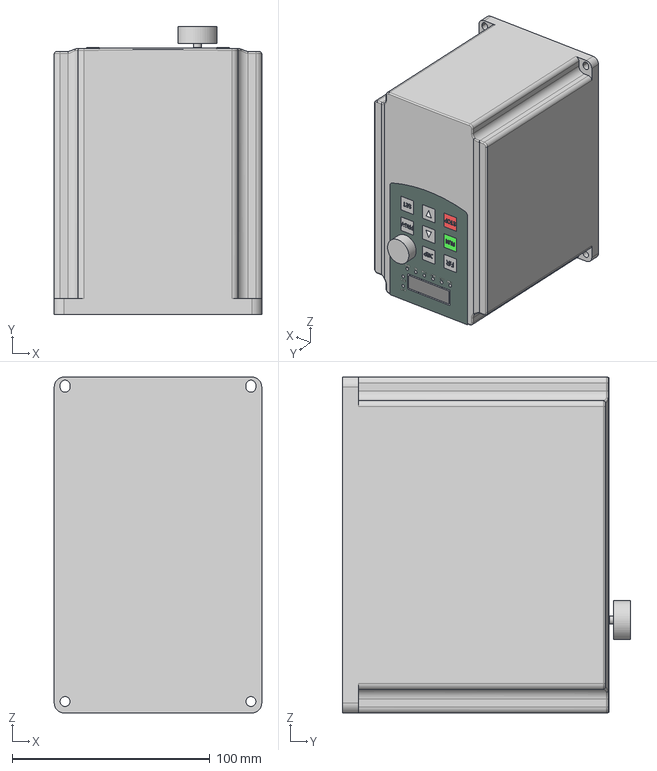
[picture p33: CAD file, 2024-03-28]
CAD files/electrical/vfd_yl620 v1.step
105.0 x 145.7 x 170.0 mm

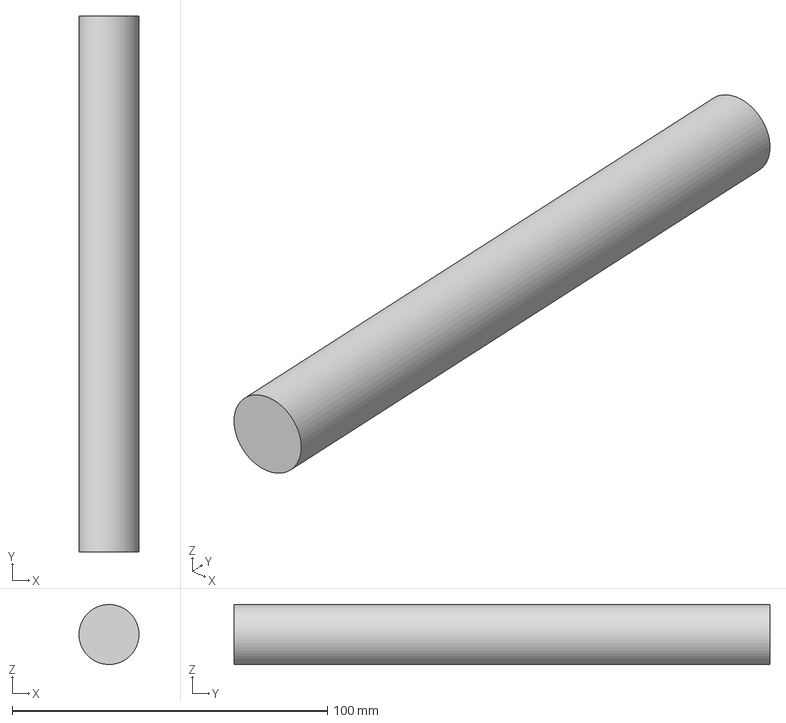
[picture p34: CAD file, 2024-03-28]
CAD files/mechanical/gear shaft v1.step
19.0 x 170.0 x 19.0 mm

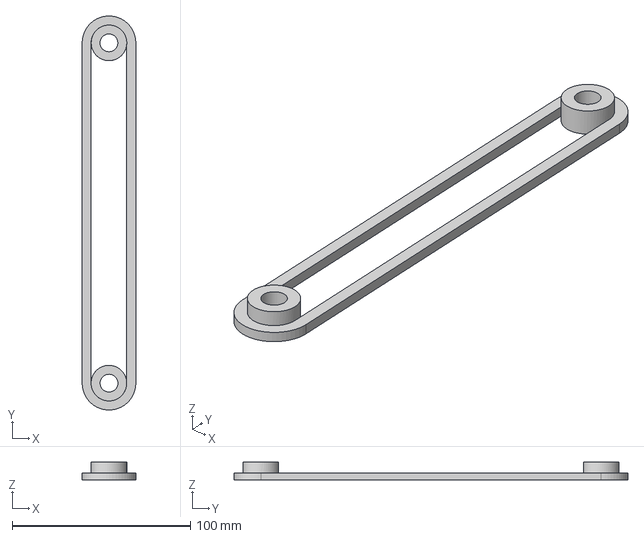
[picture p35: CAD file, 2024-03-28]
CAD files/connectors/linkage v4.step
30.2 x 221.2 x 10.0 mm

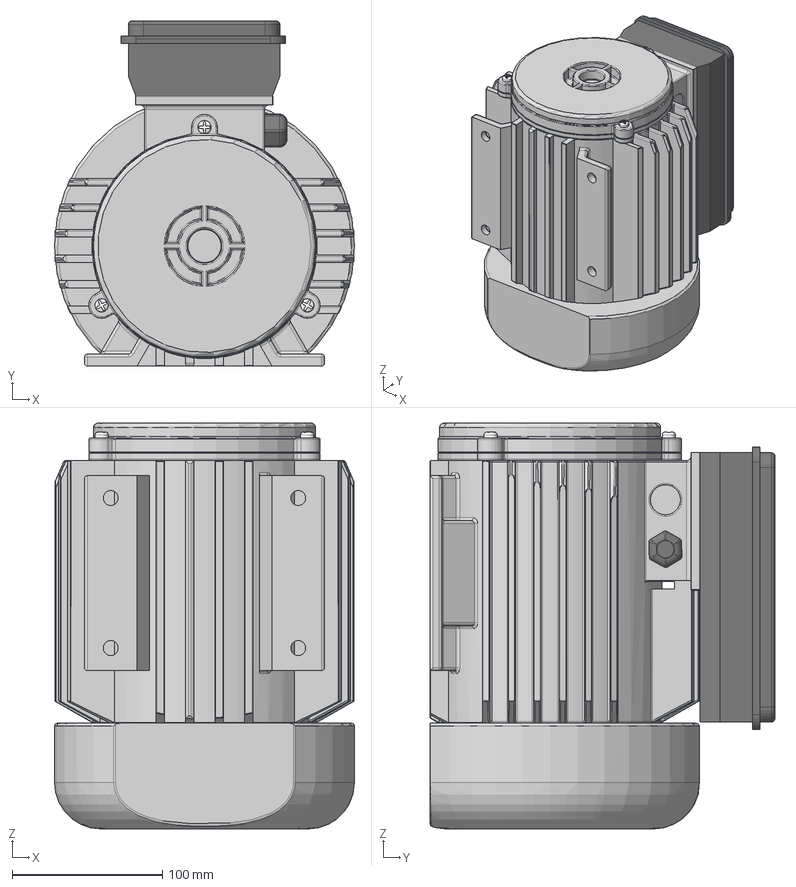
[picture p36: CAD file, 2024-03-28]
CAD files/electrical/motor v1.step
200.0 x 230.0 x 270.6 mm

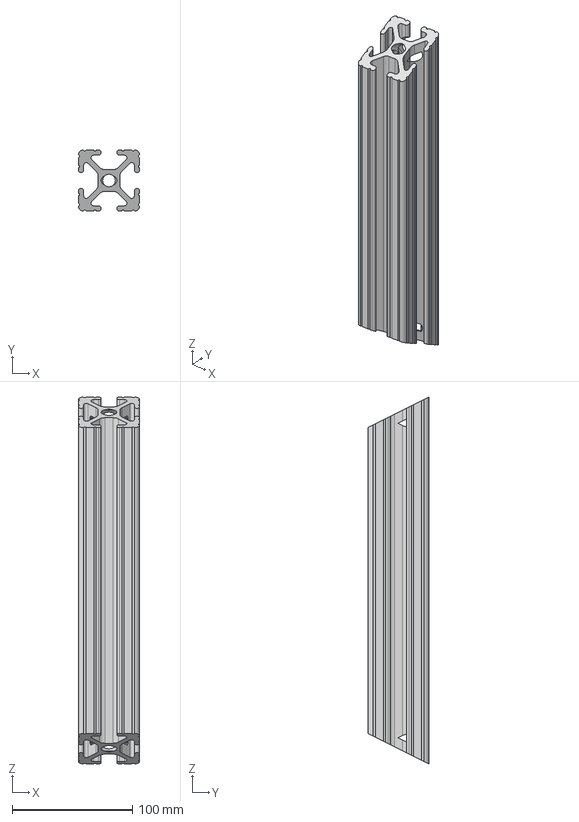
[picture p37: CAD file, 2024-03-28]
CAD files/extruded_aluminum/1 x 1 x 12 Diagonal Brace v2.step
50.8 x 50.8 x 304.8 mm

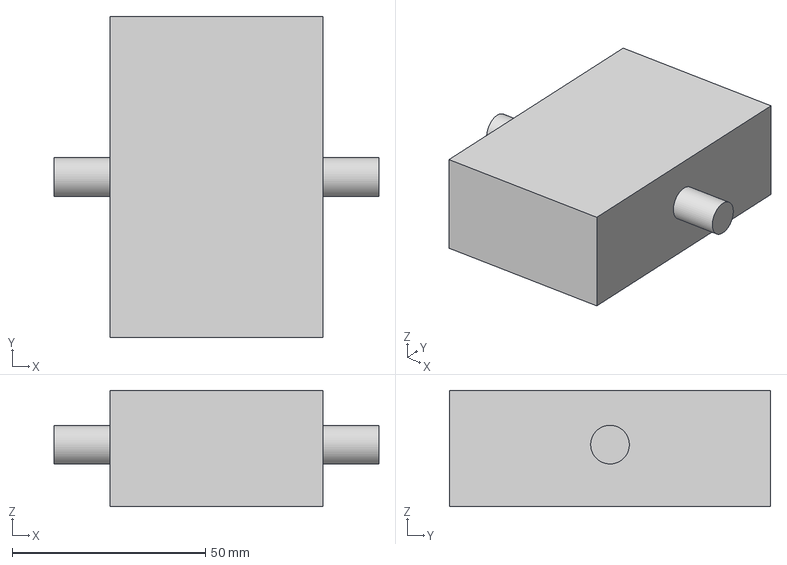
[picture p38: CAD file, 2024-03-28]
CAD files/mechanical/weight v1.step
84.0 x 83.0 x 30.0 mm

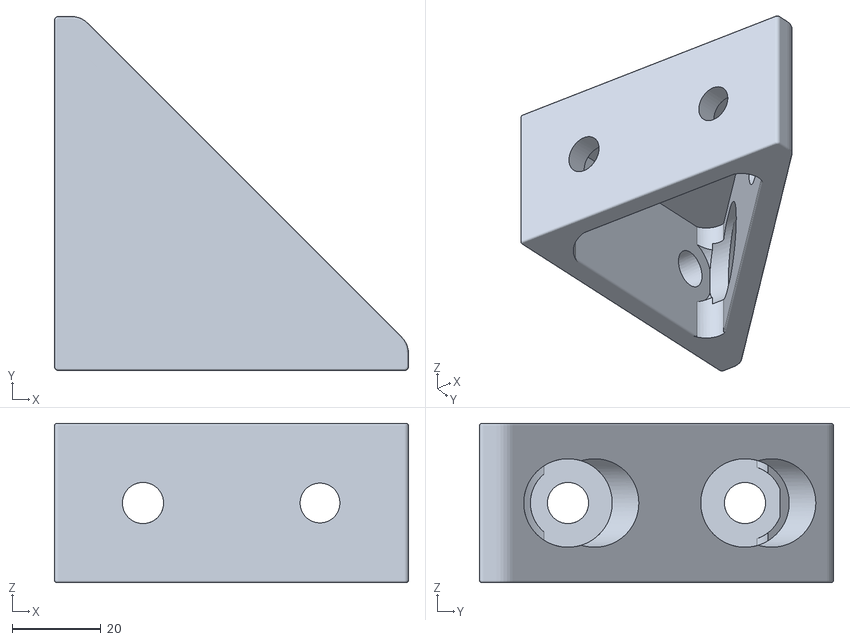
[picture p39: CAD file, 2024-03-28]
CAD files/connectors/grainger-5jru1 v7.stl
80.0 x 80.0 x 36.0

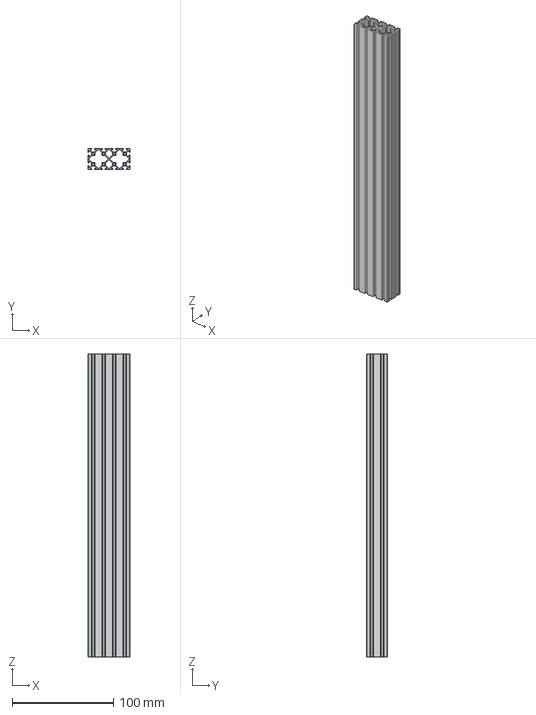
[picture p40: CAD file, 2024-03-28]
CAD files/extruded_aluminum/8020_4020 v1 v2.step
41.7 x 20.8 x 299.7 mm

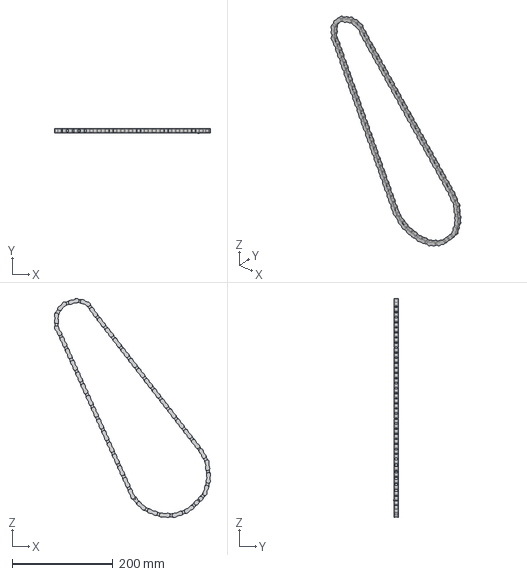
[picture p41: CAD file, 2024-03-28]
CAD files/mechanical/chain_Component1 v1.step
309.6 x 10.1 x 433.8 mm

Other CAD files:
CAD files/extruded_aluminum/extruded_aluminum_20_inch v1 v1.step
CAD files/extruded_aluminum/extruded_aluminum_30_in_f360 v2.step
CAD files/mechanical/grainger-36gc10 v1.step
CAD files/connectors/20 Two-Way Connector v12 v5.step
CAD files/connectors/grainger-5jru1 v5.stl
CAD files/extruded_aluminum/1 x 1 x 12 Diagonal Brace_half v2.step
CAD files/extruded_aluminum/8020 - 14060 v2.step
CAD files/extruded_aluminum/extruded_aluminum_15_inch v3.step
CAD files/extruded_aluminum/extruded_aluminum_20_in_f360 v2.step
CAD files/extruded_aluminum/extruded_aluminum_20_inch v4.step
CAD files/extruded_aluminum/extruded_aluminum_24_in_f360 v2.step
CAD files/extruded_aluminum/extruded_aluminum_24_inch v2.step
CAD files/extruded_aluminum/extruded_aluminum_30_inch v4.step
CAD files/mechanical/8020_rail v1.step
CAD files/mechanical/8020_roller v1.step
CAD files/mechanical/Inner Chain v1.step
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

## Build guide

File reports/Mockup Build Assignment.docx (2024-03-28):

Mockup Build

1. (0.33 pts.) Team short name (i.e., project sponsor name)
  a. Downey1
2. (0.33 pts.) Names of all team members
  a. Corinne Smith, Ryan Yount, Alex Toth, Ryan Brown
3. (0.33 pts.) Up-to-date product mission statement
  a. Dr. Austin Downey needs a bridge shaker that needs to test vibration data, operate at different frequencies, be safe to operate, and leave the bridge undamaged.
4. (1 pts.) CAD illustration of assembled product

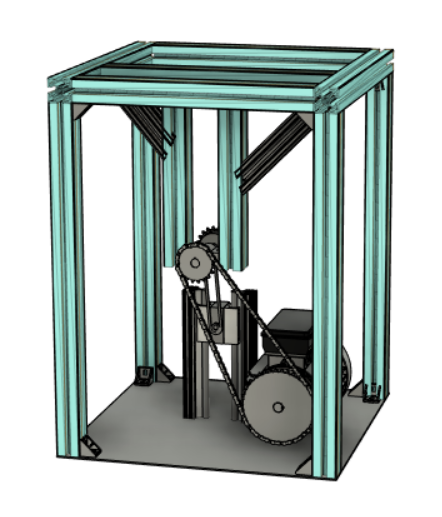
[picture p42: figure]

5. (1 pts.) Exploded view(s) of product.

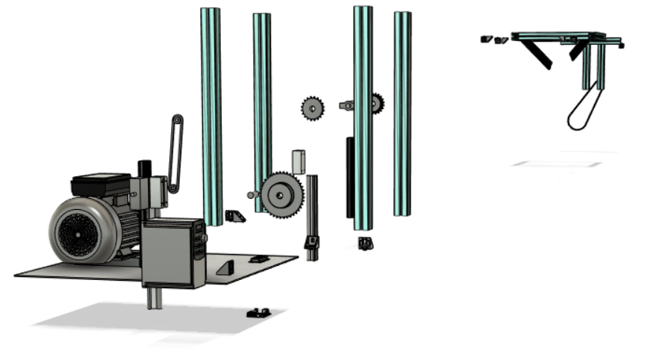
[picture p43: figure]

6. (2 pts.) Photograph(s) of final mockup build

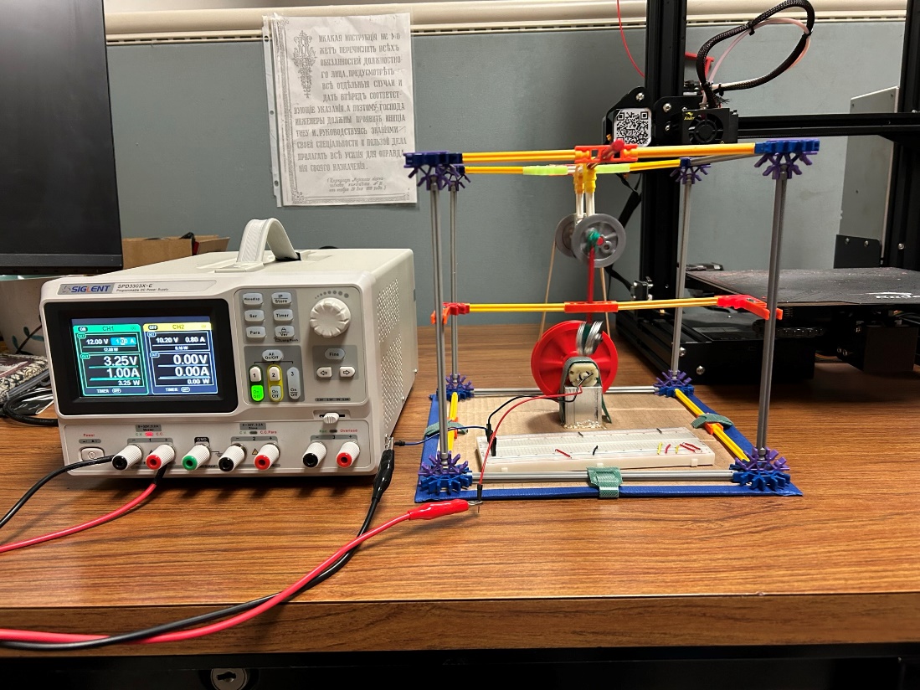
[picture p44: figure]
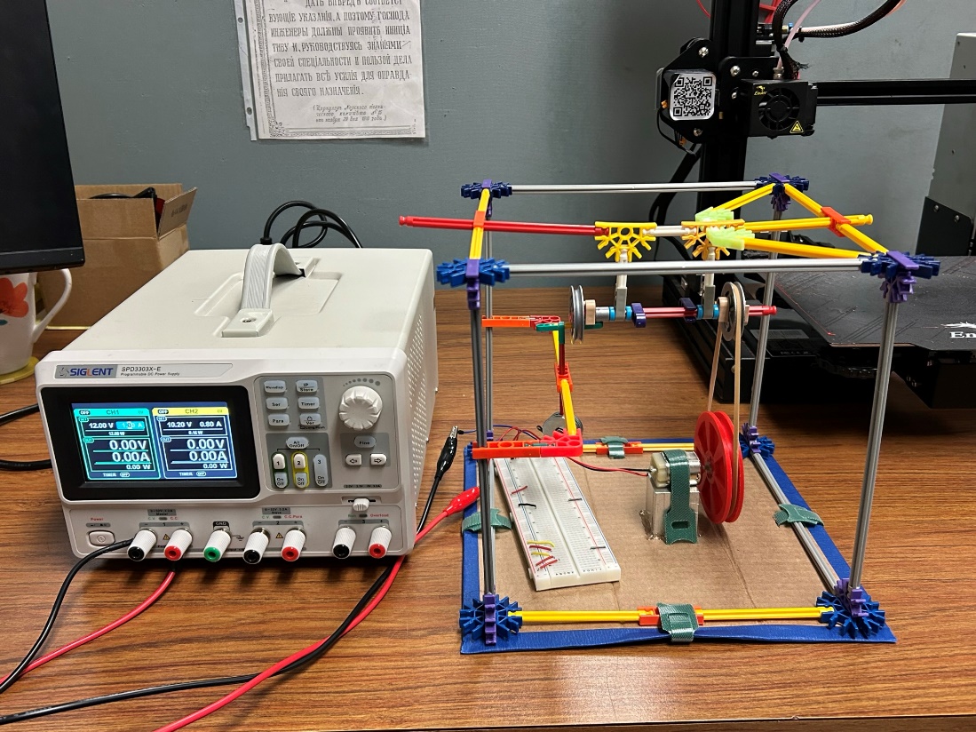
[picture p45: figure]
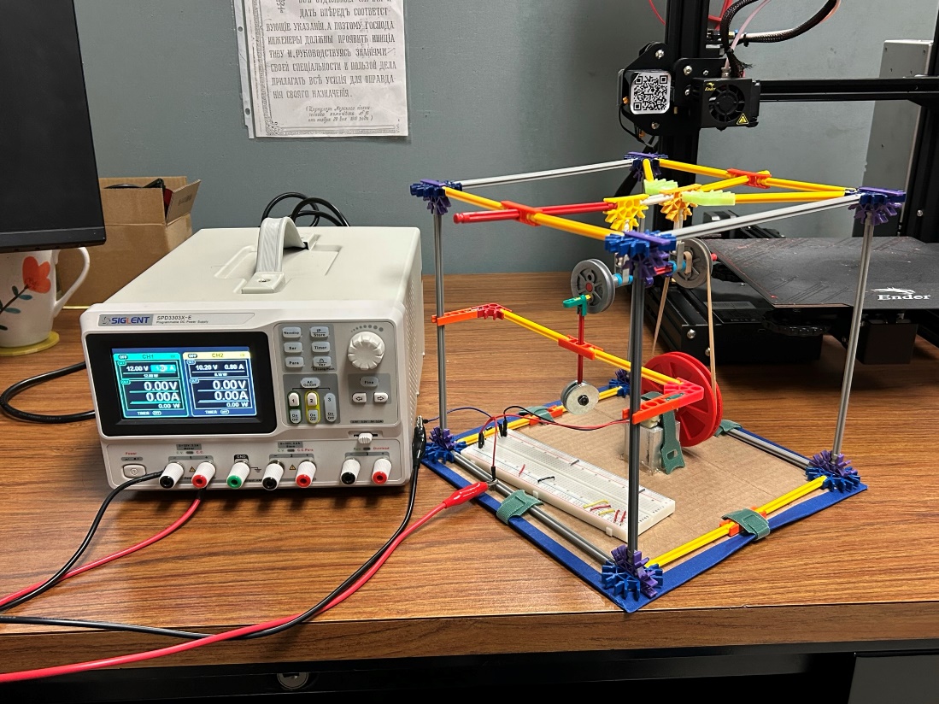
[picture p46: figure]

Our mockup in action: Mockup build in action! (https://youtu.be/3h06Zy0r7BI)

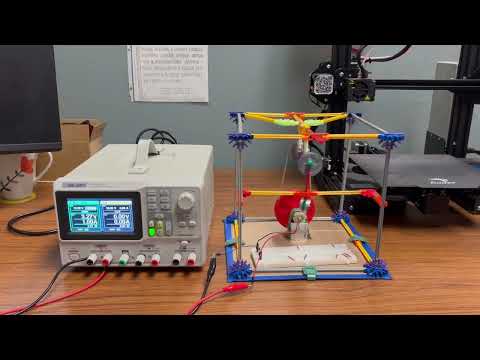
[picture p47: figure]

7. (3 pts.) Lessons learned: Explain what this build has taught you (if it is “nothing,” then you haven’t done it right!)… Are parts of the build going to pose a challenge? Do adjustments to original concept or parts need to be made? What is your confidence in the product’s success now? Will it need supplemental bracing? Can it be streamlined? Do you need to quickly find a different technology for one or more functions ? etc., etc.
  a. This build has taught the group that bracing for the shaft and weight will be critical to the success of the product. The group built a functional model using “K’nex” and a small DC motor to replicate the motion the mass shaker will go through to produce vibrations. In this experiment the group was able to pinpoint week spots in the design. This includes the shaft bracing, motor bracing under tension, the brackets holding the frame together, and the linkage connected to the weight. The original design made use of connections to the base plate for the main transfer shaft, the shaft connecting the gear to the linkage driver, but upon further investigation it was found that for ease of mounting and stability the shaft should be suspended from the top of the frame. This option allows more mobility for the shaft when discussing positioning and ease of fabrication. In addition to the shaft being suspended, it was determined by the group that the implementation of guide rails for the weight would be crucial. In the mockup build, the weight connected to the linkage exerted force in a lateral fashion and was not completely axial. For this to be fixed, a two-linkage system and guiderails will be explored to transition the energy into a more vertical manner.
  b. Another issue found from the mockup build is ensuring that the connection of the frame to the platform will not have screws or fasteners protruding on the bottom, which will hamper its ability to transfer adequate force and induce equalized vibrations to the bridge. The connections to the platform must also be strong enough to ensure stability of the frame which will hold and stabilize all moving components.
8. (2 pts.) Changes you will make to original design as result of this build (again, if your answer is “nothing” you didn’t do this correctly!). Changes you might make may include (but not limited to): sequence of the build compared to how you did this one, part geometries/positions, compacting or expanding geometries to better accommodate needs, fastener location(s), number of fasteners, sizing of functional components (e.g. pipe diameters, pumps, blowers, heat exchangers, etc.), technology to satisfy an identified function, addition of bracing, shelling solid/heavy parts, etc.
  a. Mounting tactics have been a topic of conversation of the group. The design was changed to implement a suspended mount for the shaft to reduce the footprint of the shaft bracing. With the shaft bracing, another issue came to light. The connections to the frame must be heavy duty and strong. The weight moving up and down produces a substantial amount of excess vibration and deformation in the shaker frame. This could be in part to the “K’nex” being made from a cheaper plastic material. With further research the group was able to find 80/20 40 series extruded aluminum that will suffice for the build. This material will keep the shaker in the parameters for weight while also providing more than enough strength to withstand the forces of the mechanism. The issue comes from the brackets holding the frame together. Dr. Downey encouraged the group to explore 3D printed brackets. A bracket was designed and printed for the purpose of fitment. After the fit was found to be adequate, an FEA was done on the bracket to see the displacement and stress put into the bracket. The results were within reason, therefore 3D printed brackets will be used going forward. Lastly, there was discussion about reducing the height of the contraption. The original height was slated for 2.5 FT. This was to give room for the large pinion gear that would be needed to reach the frequency specified by the sponsor. The group found a motor that would supply enough RPM to reduce the pinion size, therefore reducing the overall height.

Downey1Mockup Build Assignment1/30/23

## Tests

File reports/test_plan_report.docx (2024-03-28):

Test Plan Report

1. Introduction

The Downey1 group conducted engineering tests on the bridge shaker to evaluate its performance with respect to the target and fallback specifications, listed in Table 1. The team consulted the list of priority needs to decide the target and fallback specifications on which to perform engineering testing. It was decided that the vibration data accuracy, system output range, instrument resolution, robustness, weight, and displacement should be assessed. These were chosen because they align with the top seven needs and have specific ranges that are key to the project application. The team decided not to test any of the boolean specifications as they could not be verified through empirical engineering testing. The tests and their results are outlined in this document.

Table 1. Target and Fallback Specifications

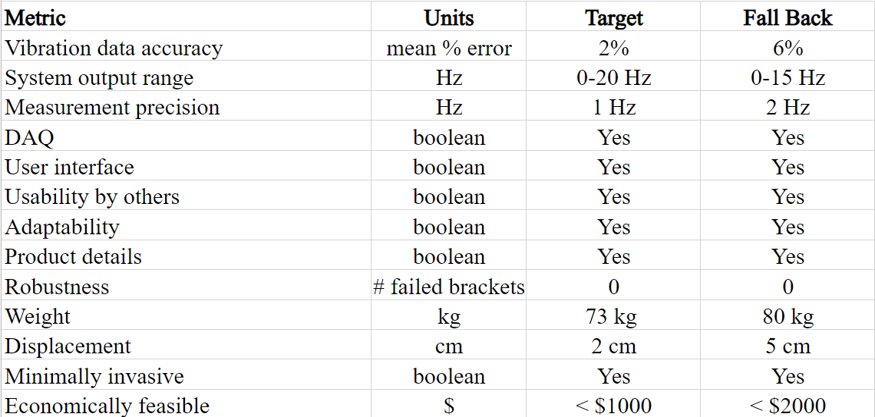
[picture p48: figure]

2. Test Methods

As previously mentioned, the parameters that will be examined in this report are vibration data accuracy, system output range, instrument resolution, robustness, weight, and displacement. There are six simple tests that need to be performed to ensure that the shaker is in good working order. The first three tests are concerned with the functional performance of the shaker as a tool for structural excitation. The first of these is to ensure that the shaker is producing accurate vibrations to excite the modal frequencies of whatever bridge or structure it has been placed on. The methodology for this test has been laid out below.

I. Test vibration data
  a. Parameter: Mean percent error
  b. Target value, Fallback value: 2%, 6%
  c. Testing Procedure: To verify that the shaker is functioning correctly to test vibration data, one PCB Piezotronics ceramic shear accelerometer and the shaker will be placed onto a pedestrian bridge, and another PCB Piezotronics ceramic shear accelerometer will be placed on the shaker. The accelerometers will report data through an NI DAQ system with an IEPE accelerometer module to LabVIEW. The shaker will be turned on, and the corresponding vibration data will be collected by the accelerometers as time domain amplitude data and will be put into the frequency domain using a Fast Fourier Transform (FFT). This test will only be performed once. The verification test will be considered successful if the accelerometers detect peaks in vibration within 2% of the specified frequency of the shaker.

The second test that must be conducted is to ensure that the shaker can operate at a range of frequencies to find the resonance frequencies of the structure. Testing this range from 0-20 Hz should be done prior to product handoff. The procedure and explanation follow.

II. Operate at different frequencies
  a. Parameter: Frequency (Hz)
  b. Target value, Fallback value: 0-20 Hz, 0-15 Hz
  c. Testing Procedure: The shaker’s output range should conform to the specifications table, which requires it to operate between 0-20 Hz. This range was chosen to ensure that the shaker has the capacity to stimulate lower frequencies that are inherent to a pedestrian bridge, particularly one that is comprised of concrete. The shaker and a PCB Piezotronics ceramic shears accelerometer will be placed onto a pedestrian bridge. A second PCB Piezotronics ceramic shears accelerometer will be placed directly onto the shaker. Once the shaker is activated, data will be read into LabVIEW from both the accelerometer on the bridge as well as the accelerometer on the shaker through a DAQ system equipped with an IEPE accelerometer module. The team will assess the functionality of the shaker once at different frequencies of 5 Hz, 10 Hz, 15 Hz, and 20 Hz, and the accelerometers will be utilized to process the resulting time domain data with an FFT. The test will be considered successful if the accelerometers read the specified peaks that are output by the shaker.

Thirdly, the shaker’s resolution must be explored. The team designed the shaker so that the shaker could operate closely to the desired frequency. The target specification was 1 Hz, but the group has experienced better control than 1 Hz. For this test, the procedure for validating high resolution is explained.

III. Resolution of at least 1 Hz
  a. Parameter: Frequency (Hz)
  b. Target value, Fallback value: ±1 Hz, ±2 Hz
  c. Testing Procedure: To test the resolution, the shaker and a PCB Piezotronics ceramic shear accelerometer will be placed on a pedestrian bridge as well as a second accelerometer of the same type on the shaker. As with previous tests, LabVIEW and a DAQ system including an IEPE module will be used to read the data from the accelerometers. The shaker will be set to 10 Hz output and allowed to stabilize at this frequency. The accelerometers will be used to verify that the shaker is at 10 Hz using an FFT on the time domain data. Then, the shaker will be set to 11 Hz and the accelerometer will be used again to verify the frequency. The test will only need to be run once as the shaker’s functionality is relatively static. If the measured frequencies match the set frequencies with a difference of 1 Hz, then the test will be deemed successful.

The next three tests focus more on the physical structure of the shaker. The first of these centers around the overall weight of the shaker. This test is very simple and requires only a scale. The shaker was designed to be easily carried by two people and then have additional weight in the form of sandbags added after the shaker is in place on the bridge. This test should only be conducted once the shaker has been assembled and then after additions or subtractions from the product have been made.

IV. Portable
a. Parameter: Weight (kg)
b. Target value, Fallback value: 73 kg, 80 kg
c. Testing procedure: The weight of the shaker must be between 73 and 80 kg, according to the target and fallback specifications table. These specifications are to allow two people to comfortably transport the shaker. The weight of the shaker will be tested using an industrial scale located in the materials test lab. The shaker will be set on the scale while turned off and the data recorded manually by reading the value, no data processing needed. The shaker will be weighed while turned off because that reflects the state in which it will be transported.

This next test should be done before, during, and after any test is performed. The shaker will inherently create forces that will strain or loosen the connections holding it together. For this reason, it is vital to the safety of the operators and the device itself that the procedures are followed well. Failures in joints could result in negative consequences to the people, shaker, or structure in the surrounding area. The procedures for checking the joints are as follows.

V. Robust
  a. Parameter: # of failed brackets
  b. Target value, Fallback value: 0 brackets, 0 brackets
  c. Testing Procedure: During testing, each of the joints will be inspected to ensure system stability. The frame is what holds everything together, and without it, the entire system could be a potential hazard. The first test will be conducted when the motor is at low speed at 5 Hz, medium speed at 10 Hz, and high speed at 15 Hz. After each test, all joints of the shaker frame and moving parts from the drive train will be inspected, as well as all fasteners to ensure they do not come loose during operation. The target and fallback specification are the same, as there is no number of failed brackets that are acceptable.

Lastly, to ensure that the shaker is transferring as much energy as possible to the bridge or structure, a test must be performed after the experimental testing is complete. If the shaker begins ‘walking’ (as described below), the shaker will be less efficient while also making the data collected far less useful. This is another very simple but very important test to the success of the shaker.

VI. Good contact to bridge
  a. Parameter: Displacement in cm
  b. Target value, Fallback value: 2 cm, 5 cm
  c. Testing Procedure: The initial and final position of the shaker after operation must have a difference no greater than 2 cm. The movement of the shaker is considered “walking. “Walking” in this sense is the movement of the shaker in the ‘X’, ‘Y’, or ‘Z’ direction. To assess the ‘X’ and ‘Y’ directions, the team will mark the initial position of the shaker on the bridge and then run a test. After the test is completed, the team can observe the total movement of the shaker over the test with a ruler or calipers. If there is significant ‘walking’ then more weight will be added to the extended legs. To observe the movement in the ‘Z’ direction (vertical in this case), the team will physically observe the shaker and ensure that it is staying down on the bridge. This test does not require data processing.

3. Analysis

After completing Tests I-III, an FFT was performed on the raw acceleration data read from the accelerometers. For each test, the sampling frequency of 2460 samples/second over a 3 second test yields 7380 raw data points. Because of this, raw data is not supplied in tabular form, but rather visually displayed in graphical form as time-domain data, shown in figure 1. In the context of vibration testing, an FFT is used to analyze and transform time-domain data, as seen in figure 1, into frequency-domain components, as seen in figures 2-6. This transformation allows the identification and visualization of the different frequencies of the structure the accelerometers are placed on. The equation for the FFT is:

F(k)=∑_()^() n=N_0 -1f(n)⋅e^((-2πi⋅k(n/N)))

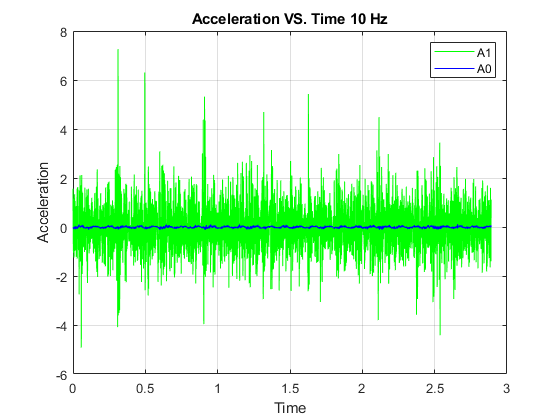
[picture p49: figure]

Figure 1: Time-domain data from 10 Hz frequency test.

The time-domain data presented above reveals a large contrast in the levels of excitation measured by the green and blue accelerometers. This can be attributed to the positioning of the accelerometers, with the green one placed directly on the shaker and the blue one placed on the bridge. Owing to its proximity to the vibration source, the green accelerometer registers a higher level of acceleration. In contrast, the blue accelerometer measures a lower acceleration as it accounts for the response of the bridge to the induced vibration.

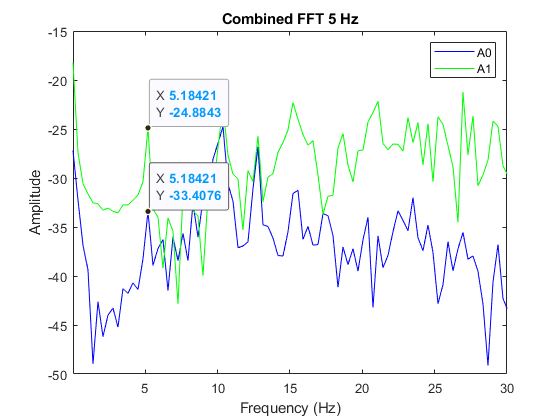
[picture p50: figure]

Figure 2: Frequency-domain data from 5 Hz test.

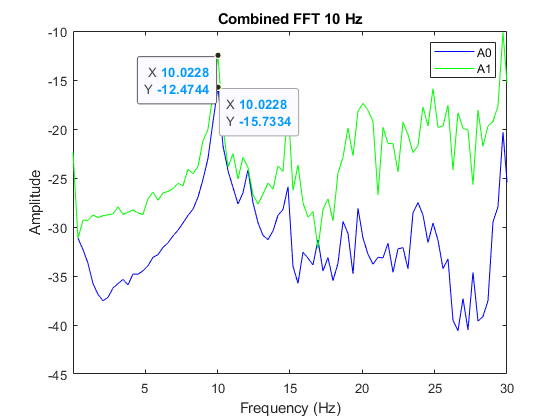
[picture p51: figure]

Figure 3: Frequency-domain data from 10 Hz test.

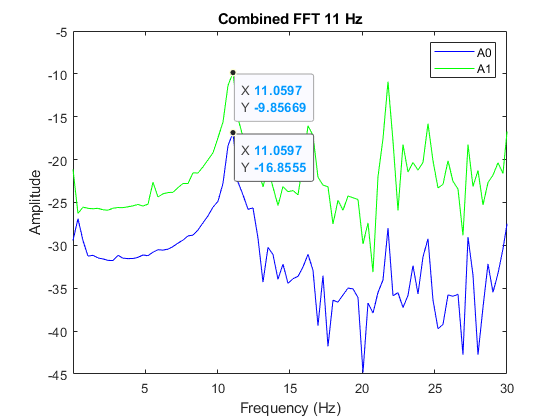
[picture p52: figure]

Figure 4: Frequency-domain data from 11 Hz test.

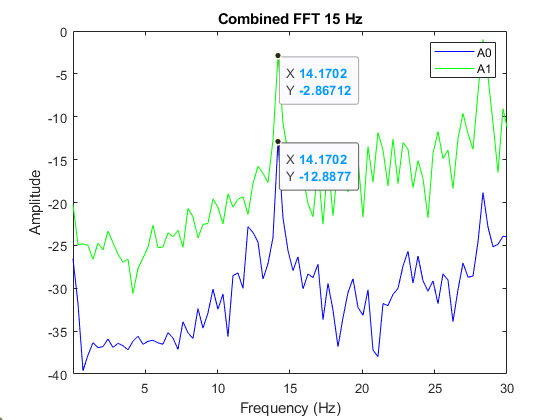
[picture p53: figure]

Figure 5: Frequency-domain data from 15 Hz test.

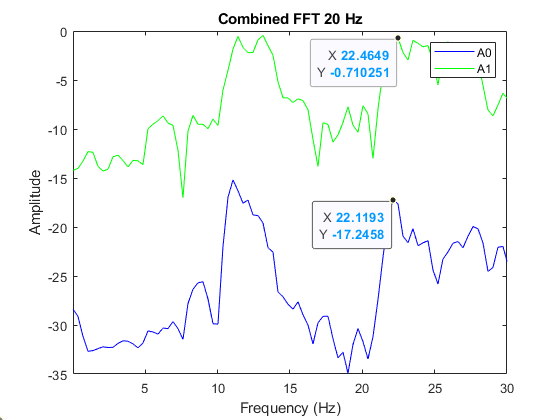
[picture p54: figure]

Figure 6: Frequency-domain data from 20 Hz test.

The results presented above demonstrate highly promising outcomes for vibration testing. The tests revealed a remarkably low mean percent error of 5.1923% for the 5, 10, 15, and 20 Hz tests. Particularly impressive were the test results at 10 and 11 Hz, exhibiting percentage errors of 0.228% and 0.543%, respectively. These outcomes are especially encouraging since the predicted first modal frequency of the bridge structure was estimated to occur around 10-11 Hz. As such, these frequencies were anticipated to produce more pronounced vibrations, leading to reduced error in the accelerometer data. With this information, the tests ran were considered acceptable for the final product.

Tests IV-VI were recorded as individual values and will be addressed individually in this report. In Test IV for portability, the recorded weight of the shaker was 50 kg, which falls far below the target value. During testing, the shaker was also transported easily with two people, satisfying the portability specification.

Test V for robustness showed that after testing in the higher frequencies, specifically at 20 Hz, multiple brackets were broken by the force of operation. After inspection, it was found that the shaft bearing had deformed from the force of operation, which resulted in the shaft oscillating vertically and inducing unexpected stress on the frame. It was theorized that this stress was what caused the brackets to fail, and the shaft bearings were changed to sturdier zinc die-cast bearings. These bearings did not deform during subsequent testing and the shaft oscillation has not been an issue, reducing the broken bracket count to zero even at high frequencies and satisfying the robustness specification.

Test VI for displacement resulted in a 19 cm displacement in the Y direction when the shaker was operated at 20 Hz, far above the 5 cm fallback value. This issue was due to too little weight holding the shaker down during operation, resulting in poor contact to the bridge. It has been addressed by adding additional sandbags on the shaker periphery, which has eliminated the displacement issue and satisfied the testing requirements. In future iterations, supports will be added to place sandbags on top of the shaker directly above the linear weight to optimize energy transfer and reduce required supplemental weight.

4. Conclusions/Recommendations

Table 2. Engineering test results compared to target and fallback specifications.

Parameter | Target value | Fallback value | Measured performance | Satisfactory? (Y/N)
Vibration Data Accuracy | 2% | 6% | 0.228% | Y
System Output Range | 0-20 Hz | 0-15 Hz | 0-15 Hz | Y
Measurement Precision | 1 Hz | 2 Hz | 1.037 Hz | Y
Portability | 73 kg | 80 kg | 50 kg | Y
Robust | 0 Failed Brackets | 0 Failed Brackets | 1+ Failed Brackets | N
Displacement | 2 cm | 5 cm | 19 cm | N

As shown in Table 2, the tests for vibration data accuracy, system output range, instrument resolution, robustness, weight, and displacement have been performed and largely satisfy the target/fallback specifications. The Boolean parameters were not tested because they corresponded to lower priority needs and were not suited for engineering performance tests. The vibration data accuracy tests ensured that the data collected lacked significant error, with a measured performance of 0.288% that satisfies the target value. The system output range test displayed the viable frequency range, which is shown to be 0-15 Hz and within the fallback specification. The measurement precision test was performed to ensure the frequency of the shaker had a resolution of 1-2 Hz, which satisfied the fallback value at 1.037 Hz. The portability of the shaker was tested based on the shaker’s weight, which should be easy to carry for two people. The total weight of the shaker was measured to be 50 kg, very far below the target specification. The robustness of the shaker was also quantified by the number of brackets broken during operation. During testing, the shaker broke several 3D printed brackets at high frequencies. Optimally, the shaker will not break any brackets, and this problem was solved by switching out the shaft bearings and opting for metal brackets. The displacement of the shaker was measured to assess unwanted movement while shaking. During testing, it moved 19 cm, and additional weight was added to address the issue and satisfy the displacement specification. At this point, the product is not yet satisfactory. While the 3D printed brackets have been replaced with much sturdier metal brackets that have not failed, the distance of the shaker traveling during operation is being solved by adding a design that allows sandbags to sit on top of the frame, better securing it to the bridge. Moving forward, the team will continue to experiment with supplemental weight to decrease the shaker’s displacement. Additionally, the team is increasing the product safety by adding expanded steel on the sides to prevent injury.

Downey1Test Plan Report and Results04/19/2023

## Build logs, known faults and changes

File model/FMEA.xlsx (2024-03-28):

· The product could disassemble itself at the connection joints under the strain of vibratory loads, with either loosening the connection bolts or completely breaking the bracket.
· Friction in the shafts could lead to underperforming.
· Friction on the guiderails could lead to underperforming.
· The guiderail system might not be strong enough to withstand the forces of the weight at max speed, causing it to break and could cause catastrophic damage to the structure. Material selection is important.
· The VFD could underperform and output less voltage than is needed for the motor.
· A fuse might trip and cut power to the system.
· The motor could overheat.
· The motor might not produce enough speed to provide adequate force to the bridge.
 | Failure Mode | Severity | Occurrence | Detection | RPN
 | A | 10 | 8 | 1 | 80
 | B | 4 | 6 | 3 | 72
 | C | 4 | 6 | 3 | 72
 | D | 10 | 9 | 5 | 450
 | E | 7 | 4 | 1 | 28
 | F | 6 | 2 | 3 | 36
 | G | 7 | 9 | 3 | 189
 | H | 7 | 4 | 2 | 56
